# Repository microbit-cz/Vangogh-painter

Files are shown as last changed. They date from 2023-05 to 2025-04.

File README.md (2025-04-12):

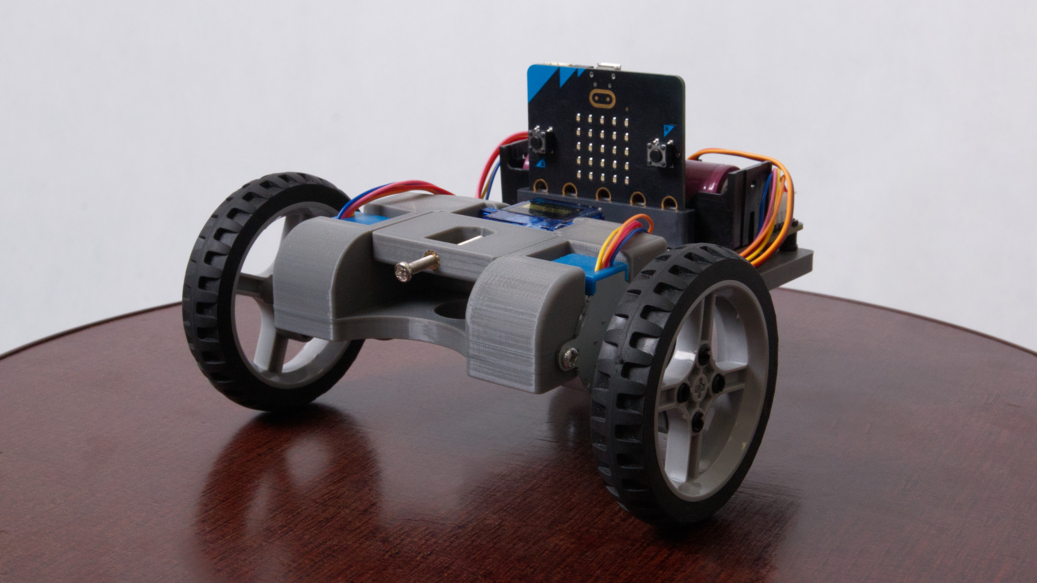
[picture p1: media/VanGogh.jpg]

<h1 align="center">VanGogh - Make art, not just ride.</h1>
<p align="center">



</p>

VanGogh is a vehicle that uses 3D printing technology, Microbit microcomputer, and lots of other components like servos and stepper motors. The final product can draw together with the <a href="https://github.com/microbit-cz/pxt-vangogh-extension" target="_blank">VanGogh extension library.</a> Hence the name VanGogh (The van that paints). Also it can be used as a quick and easy demonstration of programming.

# What do I need?
## Components
<ul>
  <li><a href="./STL" target="_blank">VanGogh construction + penholder.</a></li>
  <li><a href="https://www.printables.com/cs/model/459596-connection-hub-for-28byj-48-stepper" target="_blank">2x Adapter 6514TT 65mm lego wheel for 28BYJ-48 5V DC stepper motor.</a></li>
  <li>Micro:bit board.</li>
  <li><a href="https://www.aliexpress.com/item/1005004959920270.html" target="_blank">Motor:bit expansion board.</a></li>
  <li>2x Stepper motor 28BYJ-48 5V DC.</li>
  <li>Micro servo 9g SG90 with a lifting arm (Usually packed with servo).</li>
  <li>2x 6514TT 65mm lego wheel.</li>
  <li>9x M3 Insert with outer diameter 5mm.</li>
  <li>4x M3 screw up to 6mm, 4x up to 4mm, 2x self drilling up to 6mm and 1x at least 14mm long.</li>
  <li><a href="./media/supportwheel.jpg">Support wheel</a>. (aka <a href="https://www.aliexpress.com/item/1005006350270276.html">this</a>, <a href="https://www.aliexpress.com/item/1005006452380644.html">this</a>, or <a href="https://www.aliexpress.com/item/32572389926.html">this</a>)</li>
  <li>12x Lego pin 2780.</li>
  <li><a href="https://github.com/microbit-cz/pxt-vangogh-extension" target="_blank">VanGogh extension library.</a></li>
</ul>

## Prerequisites
<li>3D printer with minmal 15x15 cm printing space.</li>
<li>22 meters of your favorite filament (Tested on PLA).</li>
<li>Solder for easy installation of inserts.</li>

Before printing, I would recommend measuring the diameter of the writing utensil you want to use (I recommend a marker) and lengthen or shorten the insert "VanGoghPenHolderInsert" accordingly.

# Assembly
<ol>
  <li>Insert the inserts with a solder into the holes provided for them (they are on the sides next to the holes for the stepper motors and 4 from the bottom on the platform for the board. One insert also belongs to the penholder, you can see in the picture)</li>
  <li>Together with the penholder insert the servo motor with lifting arm into the construction and screw the motor with self-drilling screws M3.</li>
  <li>Insert the stepper motors into the structure and screw them with longer M3 screws (up to 6mm).</li>
  <li>Attach the adapters to the wheels with Lego pins and then fit in the stepper motors.</li>
  <li>Screw the support wheel into the structure with shorter M3 screws (up to 4mm).</li>
  <li>Insert the Lego pins into the structure and mount the board (I recommend to squeeze the cables under the board).</li>
  <li>Connect the servo to the pins marked S1 <b>(brown wire to the black pin).</b></li>
  <li>Connect the steppers to their connectors on the same side (right stepper to the connector on the right side).</li>
  <li>Insert the printed insert into the penholder, insert pen and attach with the longest M3 screw (at least 14mm).</li>
</ol>

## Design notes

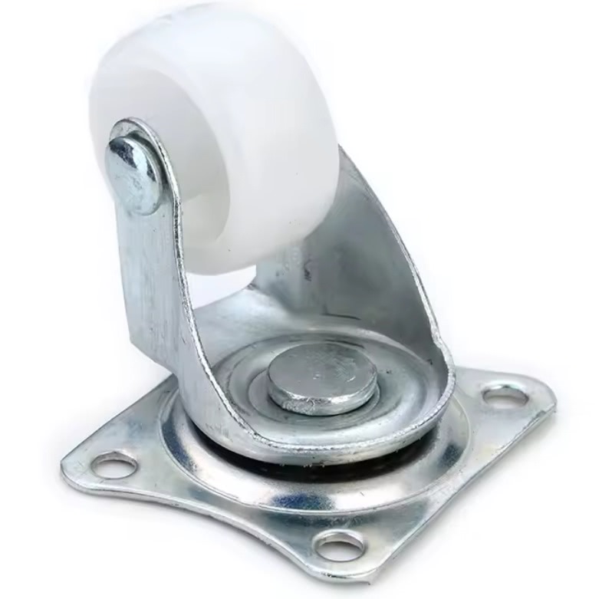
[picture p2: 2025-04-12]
media/supportwheel.jpg

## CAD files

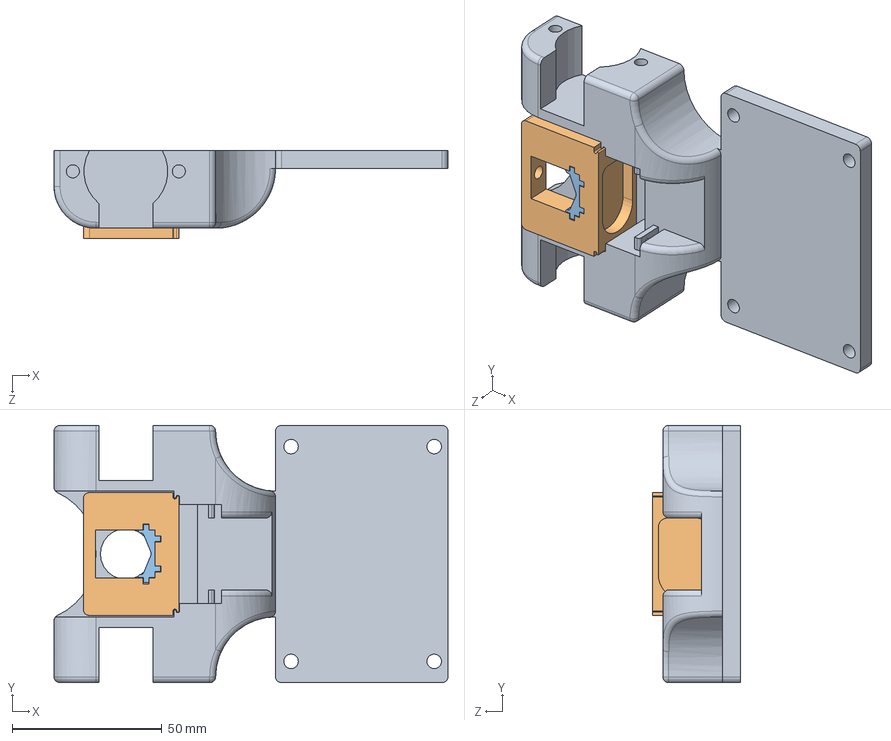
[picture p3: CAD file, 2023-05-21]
SLD/VanGogh.SLDASM
131.6 x 86.0 x 29.5 mm
VanGoghBody
VanGoghPenHolder
VanGoghPenHolderInsert

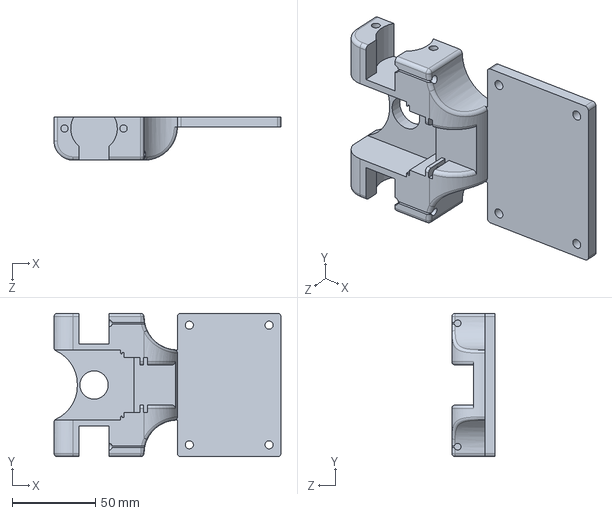
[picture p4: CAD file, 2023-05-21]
SLD/VanGoghBody.SLDPRT
136.1 x 86.0 x 26.0 mm

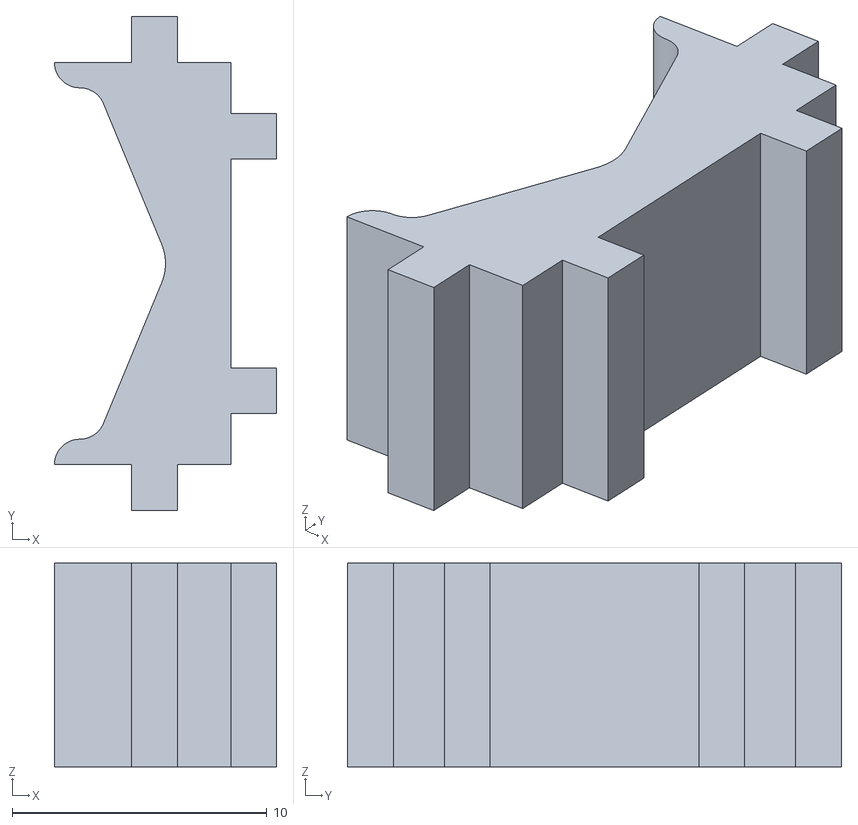
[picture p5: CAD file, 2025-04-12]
STL/VanGoghPenHolderInsert24.STL
8.73 x 19.4 x 8.00

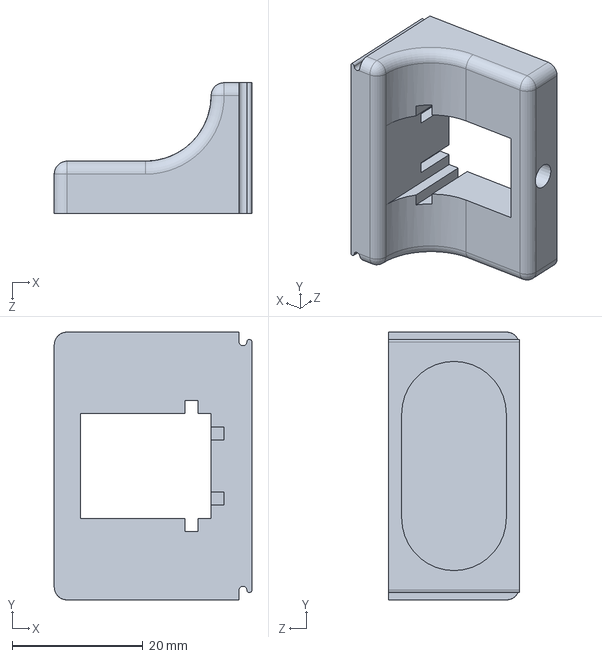
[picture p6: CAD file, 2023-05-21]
SLD/VanGoghPenHolder.SLDPRT
30.2 x 41.0 x 20.0 mm

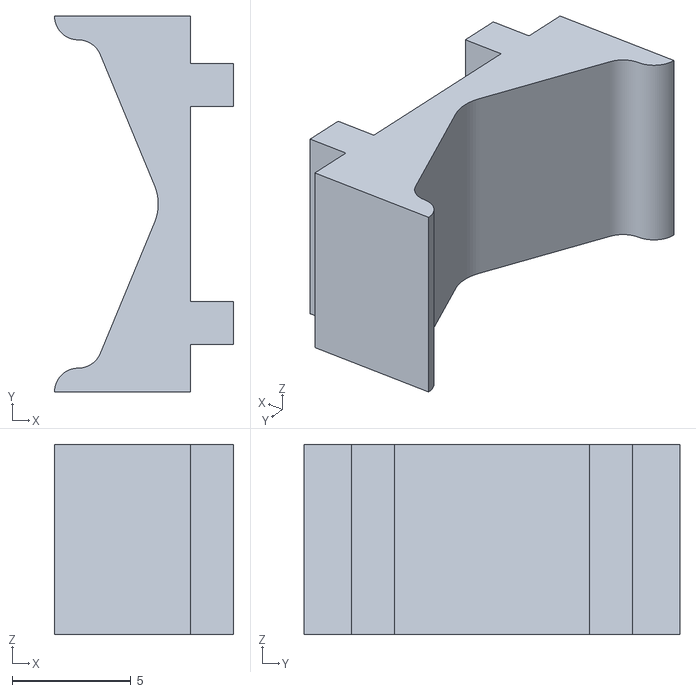
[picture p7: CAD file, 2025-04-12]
STL/VanGoghPenHolderInsert12.STL
7.53 x 15.8 x 8.00

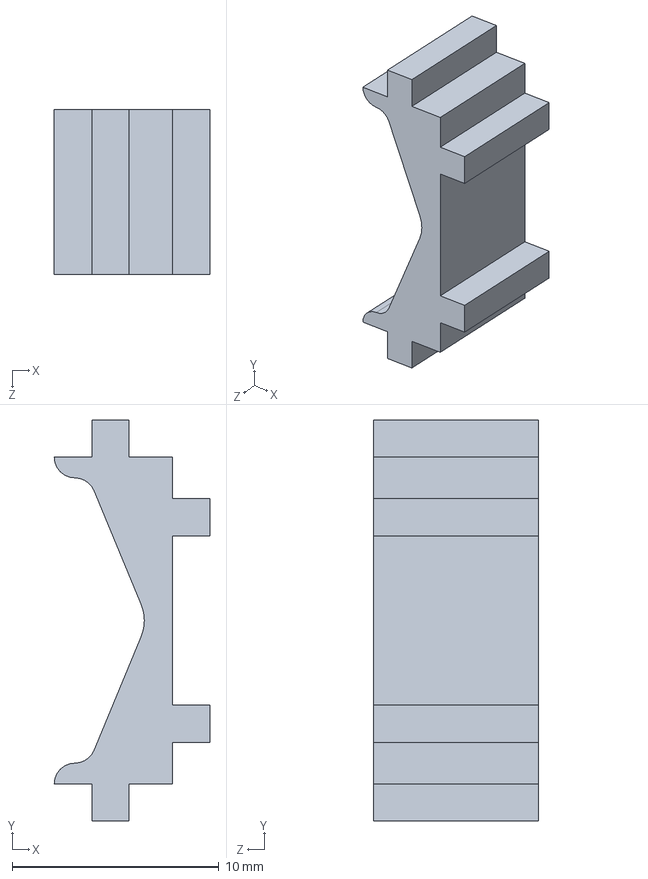
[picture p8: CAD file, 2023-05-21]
SLD/VanGoghPenHolderInsert.SLDPRT
7.53 x 19.4 x 8.00 mm

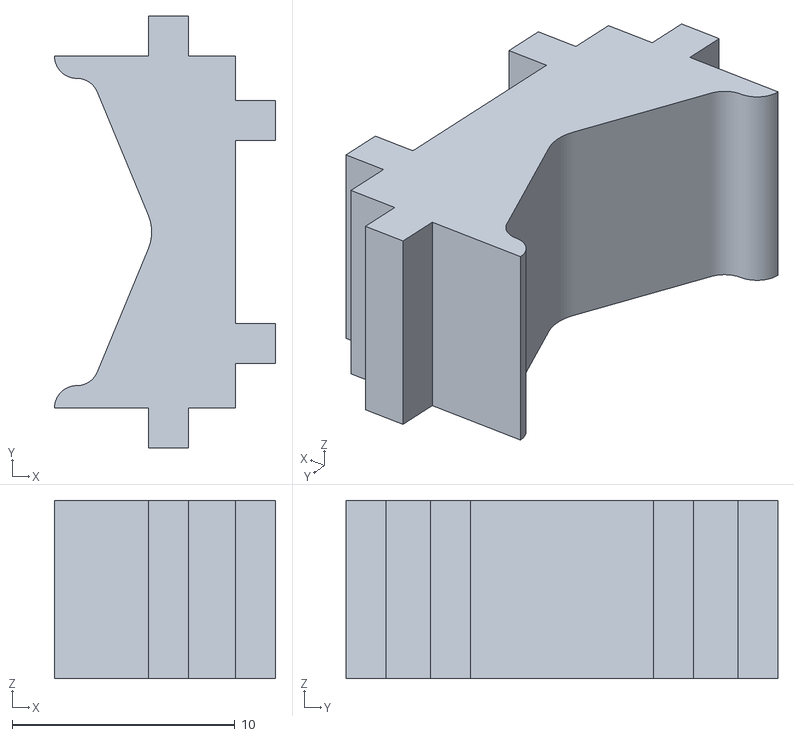
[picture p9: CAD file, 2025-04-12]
STL/VanGoghPenHolderInsert36.STL
9.93 x 19.4 x 8.00

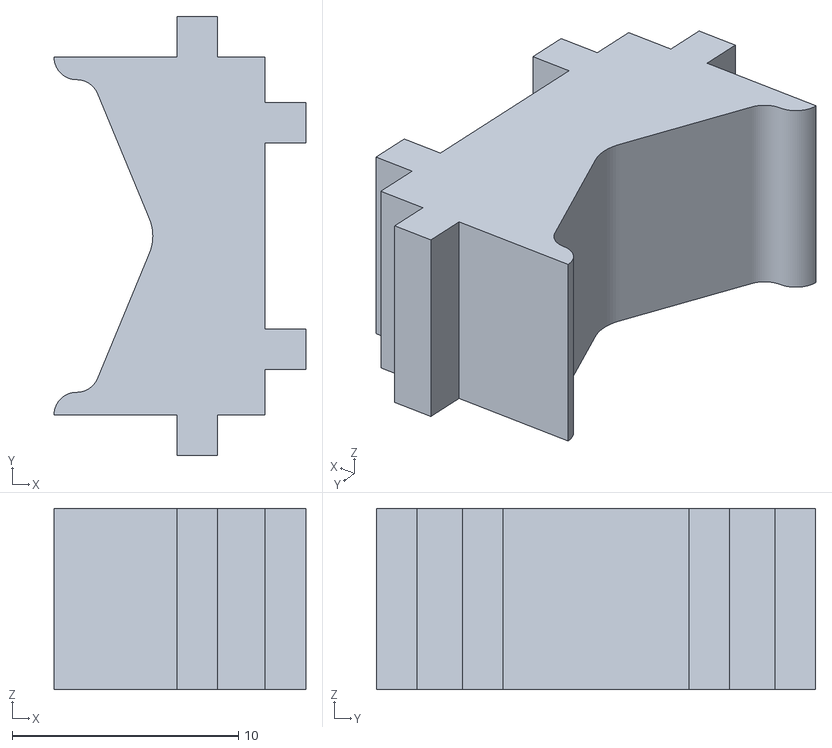
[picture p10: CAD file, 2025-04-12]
STL/VanGoghPenHolderInsert48.STL
11.1 x 19.4 x 8.00

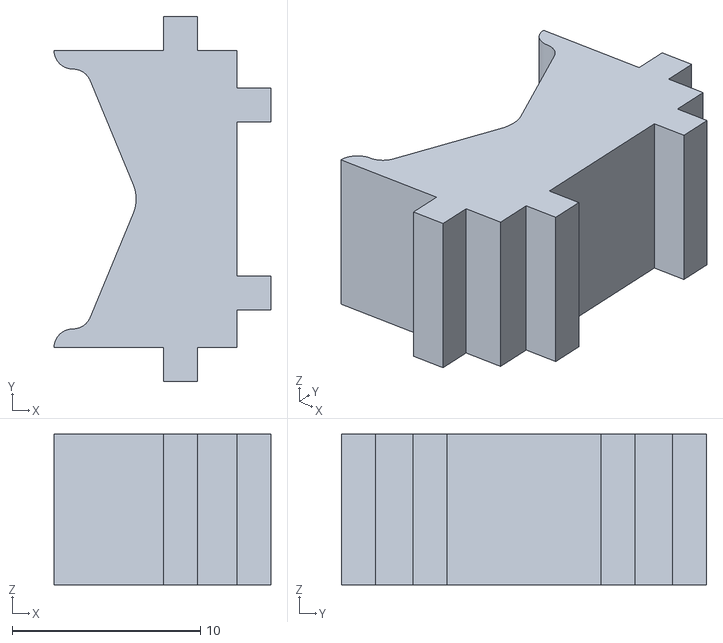
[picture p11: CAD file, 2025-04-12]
STL/VanGoghPenHolderInsert52.STL
11.5 x 19.4 x 8.00

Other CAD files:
STL/VanGoghPenHolderInsert.STL
STL/VanGoghBody.STL
STL/VanGoghPenHolder.STL

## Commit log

2023-05-03 Přidáno tělo VanGogha
    [VanGoghBody.SLDPRT]
2023-05-03 Přidán držák tužky a přizpůsobení konstrukce.
    [VanGogh.SLDASM, VanGoghBody.SLDPRT, VanGoghPenHolder.SLDPRT]
2023-05-03 Upraven otvor ramena serva na držáku
    [VanGoghPenHolder.SLDPRT]
2023-05-03 Upraveny otvory na uchycení serva
    [VanGoghBody.SLDPRT]
2023-05-04 Opraven otvor na rameno servo
    [VanGoghPenHolder.SLDPRT]
2023-05-09 Rozpracována lepší verze
    [VanGoghBodyTodo.SLDPRT]
2023-05-09 Todo cable management
    [VanGoghBody.SLDPRT]
2023-05-09 Nejlepší otvor?!
    [VanGoghPenHolder.SLDPRT]
2023-05-11 Prodlouženy otvory na inserty
    [VanGoghBody.SLDPRT]
2023-05-21 Cable management a otvor pro rameno serva
    [VanGoghBody.SLDPRT, VanGoghPenHolder.SLDPRT]
2023-06-05 Stl + dokumentace
    [VanGoghBody.STL, VanGoghPenHolder.STL, VanGoghPenHolderInsert.STL]
2025-04-12 different sizes of inserts
    [VanGoghPenHolderInsert12.STL, VanGoghPenHolderInsert24.STL, VanGoghPenHolderInsert36.STL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]
2025-04-12 support wheel example

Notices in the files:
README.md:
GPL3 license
